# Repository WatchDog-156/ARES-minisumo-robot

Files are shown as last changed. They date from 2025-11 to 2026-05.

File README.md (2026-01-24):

# ARES – Autonomiczny Robot Elektroniczny Sumo

Projekt autonomicznego robota minisumo, budowanego w ramach zajęć z przedmiotu Sterowniki Robotów. Robot przeznaczony jest do rywalizacji na arenie zgodnej z regulaminem Robotic Arena.

---

## Spis treści
- [Opis projektu](#opis-projektu)
- [Architektura systemu](#architektura-systemu)
- [Konfiguracja mikrokontrolera](#konfiguracja-mikrokontrolera)
- [Urządzenia zewnętrzne](#urządzenia-zewnętrzne)
- [Projekt elektroniki](#projekt-elektroniki)
- [Konstrukcja mechaniczna](#konstrukcja-mechaniczna)
- [Oprogramowanie](#oprogramowanie)

---

## Opis projektu

Głównym celem projektu jest zbudowanie w pełni autonomicznego robota mobilnego klasy **MiniSumo**, którego podstawowym zadaniem jest wykrycie przeciwnika na arenie, szybkie dotarcie do niego i wypchnięcie poza białą linię ograniczającą ring. Robot jednocześnie musi samodzielnie unikać wyjechania poza obszar walki.

Robot wykorzystuje system czujników:
- **Czujniki białej linii** – do detekcji krawędzi areny
- **Czujniki odległości IR (ToF)** – do lokalizacji przeciwnika
- **System ASS (Anti-Sumo System)** – serwomechanizmy z białymi ekranami, wprowadzające przeciwnika w błąd

---

## Architektura systemu

System składa się z trzech głównych warstw:

1. **Warstwa sprzętowa** – mikrokontroler, czujniki, silniki, sterowniki, zasilanie
2. **Warstwa sterowania** – oprogramowanie na Raspberry Pi Pico
3. **Warstwa komunikacji** – USART (Bluetooth) do debugowania i monitorowania

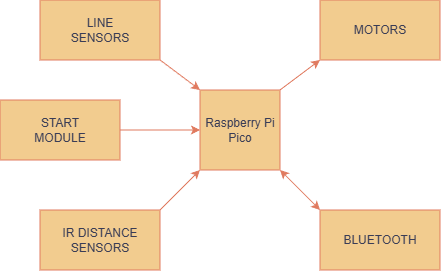
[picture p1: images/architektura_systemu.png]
Architektura systemu


---

## Konfiguracja mikrokontrolera

W projekcie wykorzystano **Raspberry Pi Pico 2 WH** z układem RP2350 (ARM Cortex M33), który oferuje:
- Dwa rdzenie obliczeniowe
- Wbudowany moduł WiFi/Bluetooth (CYW43439)
- Wystarczającą liczbę pinów GPIO
- Niskie zużycie energii

### Konfiguracja pinówdotarcie

| Pin | Tryb pracy | Funkcja |
|-----|---|---|
| 1 | USART0 TX | Wysyłanie danych Bluetooth |
| 2 | USART0 RX | Odbieranie danych Bluetooth |
| 10  | GPIO_Output | Silnik lewy – kierunek "do przodu" |
| 11  | GPIO_Output | Silnik lewy – kierunek "do tyłu" |
| 12  | PWM | Silnik lewy – sygnał PWM |
| 14  | PWM | Silnik prawy – sygnał PWM |
| 15  | GPIO_Output | Silnik prawy – kierunek "do tyłu" |
| 16  | GPIO_Output | Silnik prawy – kierunek "do przodu" |
| 19  | GPIO_Input | Start walki (przycisk/modul startowy) |
| 20  | GPIO_Input | Kill (koniec walki) |
| 21  | GPIO_Output | XSHUT 1 – włącznik czujnika odległości 1 |
| 22  | GPIO_Output | XSHUT 2 – włącznik czujnika odległości 2 |
| 24  | GPIO_Output | XSHUT 3 – włącznik czujnika odległości 3 |
| 25  | GPIO_Output | XSHUT 4 – włącznik czujnika odległości 4 |
| 26  | I2C0 SDA | Dane z czujników odległości IR |
| 27  | I2C0 SCL | Zegar czujników odległości IR |
| 31  | ADC_IN | Prawy czujnik linii (analogowy) |
| 32  | ADC_IN | Lewy czujnik linii (analogowy) |

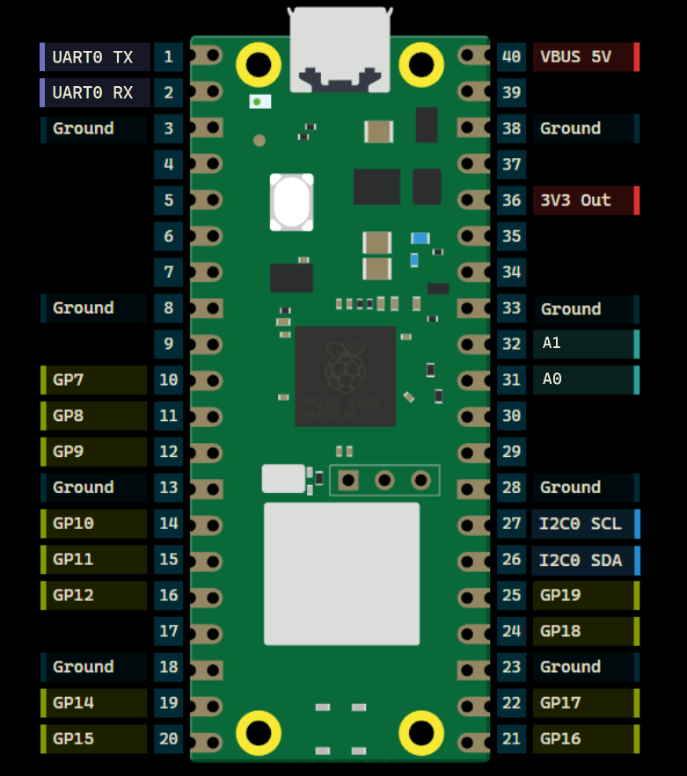
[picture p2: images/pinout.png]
Raspberry Pi Pico 2 WH pinout


### Konfiguracja peryferiów

#### USART (Bluetooth)
- Baud Rate: 115200
- Word Length: 8 bitów
- Parity: Brak
- Stop Bits: 1

#### I2C (czujniki VL53L0X)
- Tryb: Standard Mode
- Częstotliwość: 100 kHz
- Adresowanie: 7-bitowe

#### ADC (czujniki linii)
- Rozdzielczość: 12 bitów
- Tryb: Single Conversion
- Częstotliwość próbkowania: 96 cykli

---

## Urządzenia zewnętrzne

### 3.1 Czujniki białej linii – KTIRO711S
- **Zasilanie:** 5V
- **Wyjście:** analogowe
- **Rodzaj:** odbiciowy fototranzystorowy
- **Rozdzielczość:** 1 mm
- **Zastosowanie:** detekcja białej linii areny

### 3.2 Czujniki odległości IR – VL53L0X
- **Zasilanie:** 3.3 – 5V
- **Zakres pomiarowy:** 2 – 200 cm
- **Częstotliwość odczytu:** do 50 Hz
- **Interfejs:** I2C
- **Kąt widzenia:** 25° stożkowy
- **Ilość:** 4 szt. (2 przednie, 2 skośne)

### 3.3 Sterownik silników – TB6612FNG
- **Napięcie silników:** do 15V
- **Napięcie logiczne:** 2.7 – 5.5V
- **Prąd ciągły:** 1.2A na kanał
- **Prąd szczytowy:** 3.2A
- **Tryby:** CW, CCW, hamulec, stop

### 3.4 Silniki DC – N20-BT37 210:1 140RPM
- **Napięcie:** 3 – 9V
- **Przekładnia:** 210:1
- **Prędkość:** 140 RPM
- **Moment obrotowy:** 3.6 kg·cm

### 3.5 Serwomechanizmy – MG90S Mikro (ASS)
- **Napięcie:** 4.8V
- **Kąt obrotu:** 180°
- **Moment:** 2 kg·cm
- **Zastosowanie:** system wprowadzania w błąd przeciwnika

### 3.6 Moduł startowy MiniSumo
- **Funkcja:** detekcja startu walki
- **Zapobiega falstartom**
- **Wymagany na zawodach**

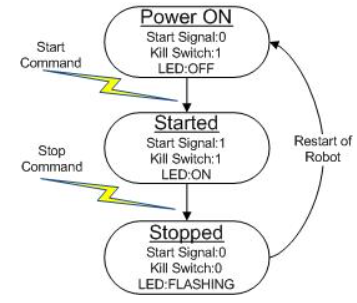
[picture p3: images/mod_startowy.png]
Moduł startowy


---

## Projekt elektroniki

Zaprojektowano dedykowaną płytkę PCB w formie shielda dla Raspberry Pi Pico, która integruje wszystkie komponenty:

### Główne cechy projektu:
- Zasilanie z baterii LiPo 7.4V
- Stabilizator napięcia 5V dla logiki i czujników
- Filtracja napięć i zabezpieczenia przeciwprzepięciowe
- Wyprowadzenia dla wszystkich czujników i silników
- Łatwy montaż na robocie

### Schematy i projekty:

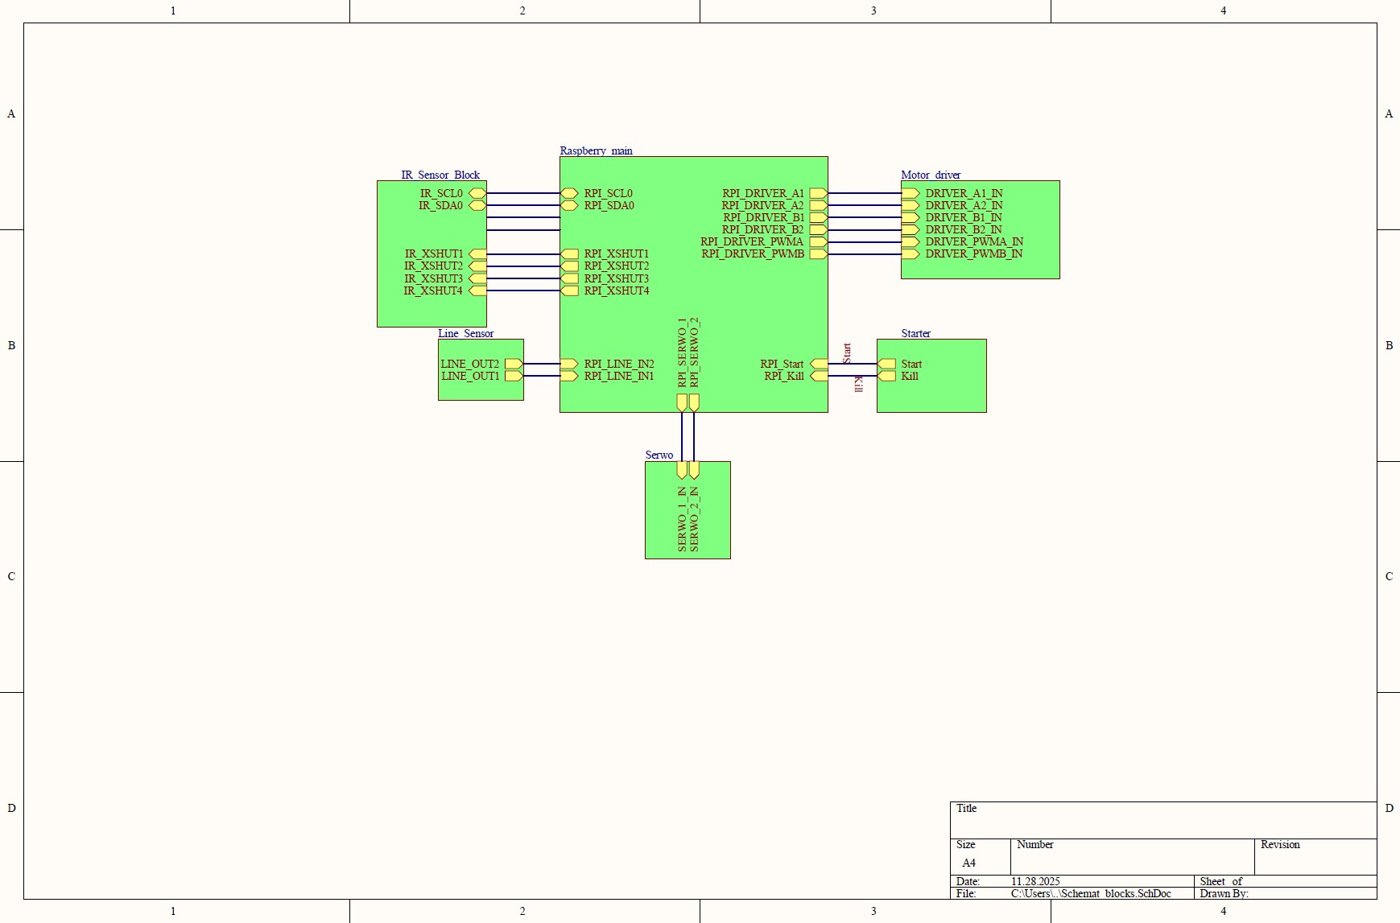
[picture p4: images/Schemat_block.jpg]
Schemat blokowy PCB


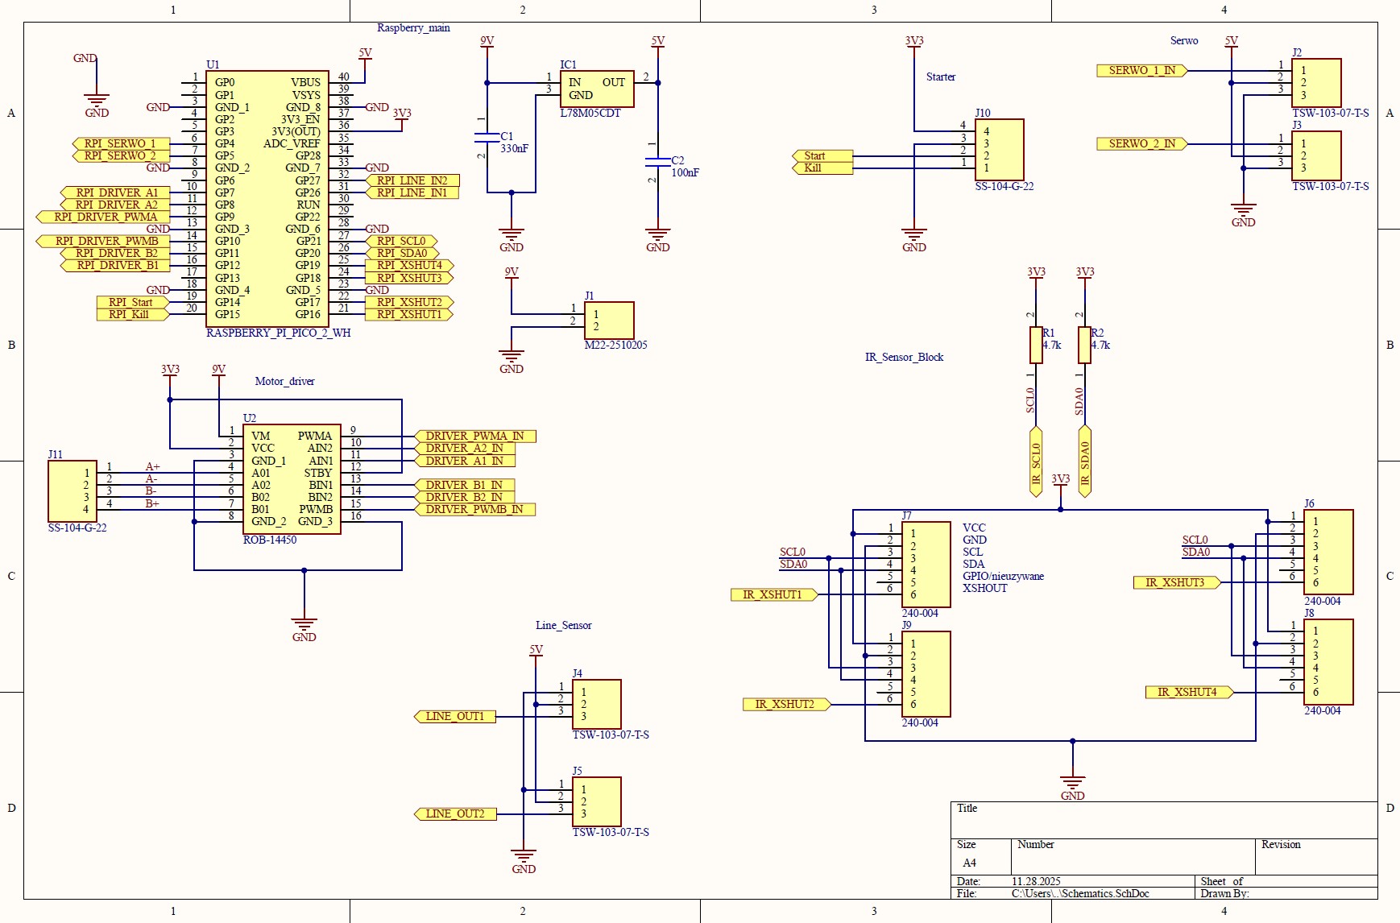
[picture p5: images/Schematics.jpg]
Schemat elektroniczny


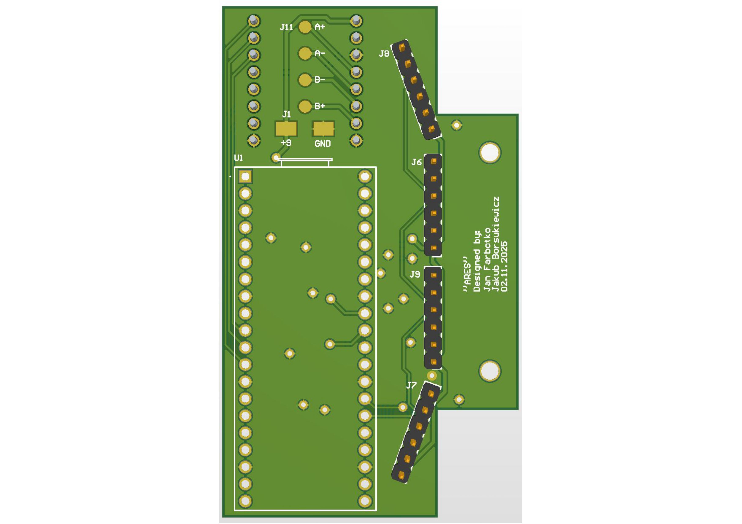
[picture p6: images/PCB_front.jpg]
Projekt PCB – warstwa górna


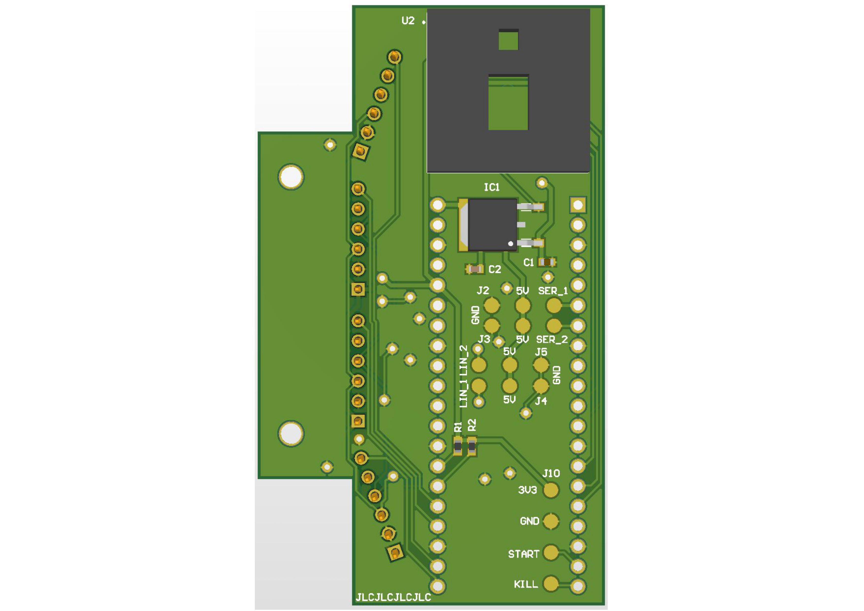
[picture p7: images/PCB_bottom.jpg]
Projekt PCB – warstwa dolna


### Montaż i lutowanie:

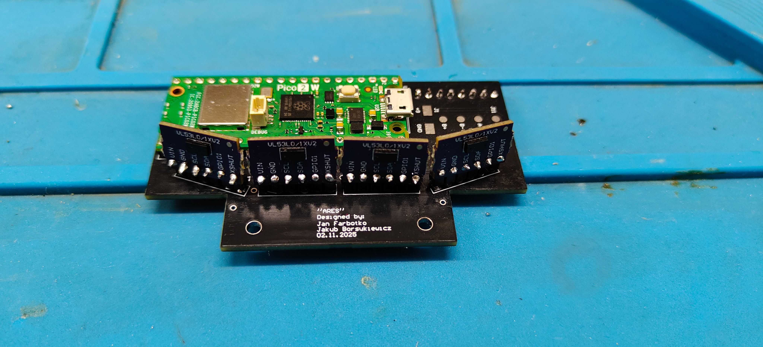
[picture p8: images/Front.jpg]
PCB po lutowaniu – przód


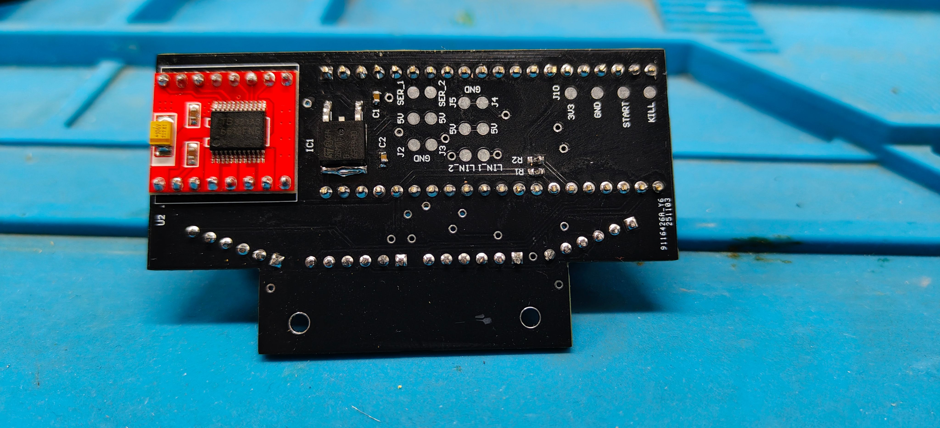
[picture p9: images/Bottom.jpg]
PCB po lutowaniu – tył


---

## Konstrukcja mechaniczna

### Projekt CAD
Konstrukcja zaprojektowana w **Autodesk Inventor**, składa się z:
- Głównej obudowy (korpus)
- Pokrywy górnej
- Dwóch części plugów
- Kół z felgami 3D i oponami silikonowymi

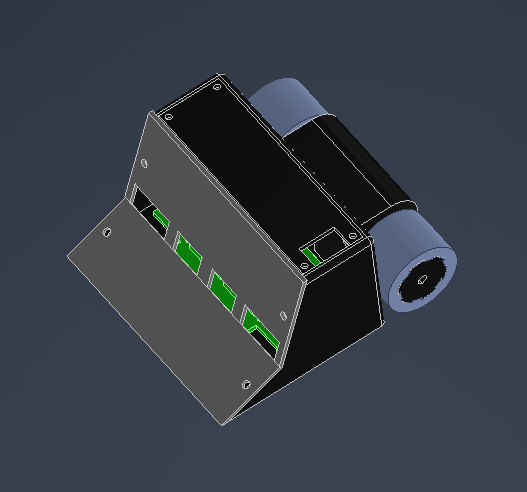
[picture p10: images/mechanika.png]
Model 3D robota


### Produkcja
- Wydruk 3D z filamentu PET-G
- Wstawki mosiężne do mocowania
- Śruby metalowe M3 oraz M2.5
- Opony z silikonu formierskiego

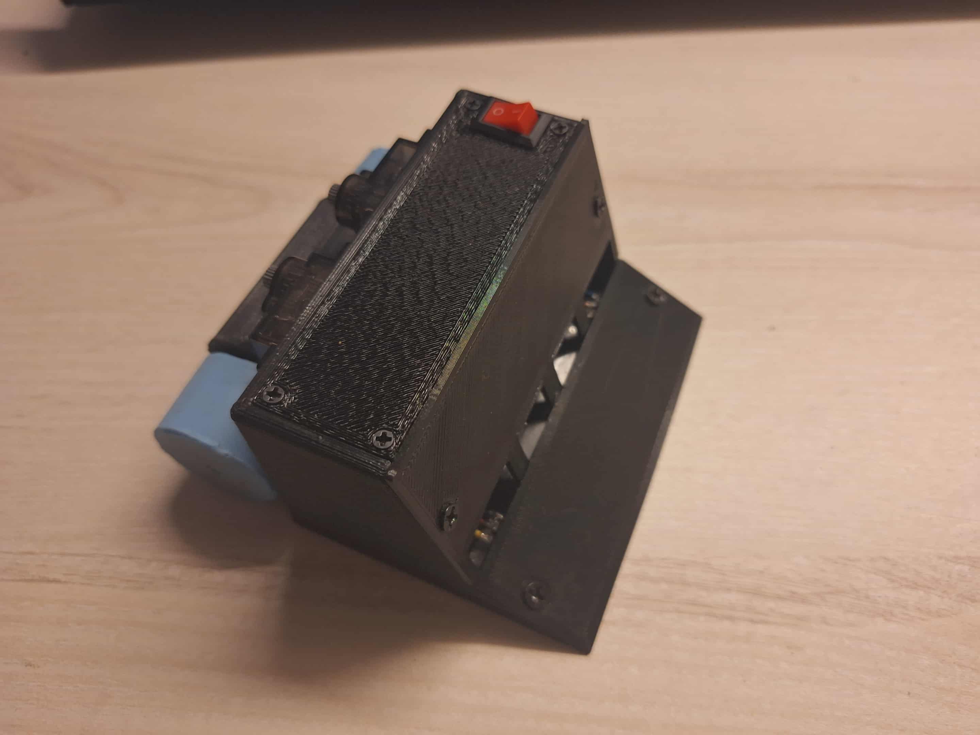
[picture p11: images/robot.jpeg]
Gotowy robot


---

## Oprogramowanie

Głównym zadaniem działania programu dla robota minisumo jest realizacja autonomicznego cyklu walki. Robot ma za zadanie odpowiednio przetwarzać otrzymywane dane z czujników odległości i linii, na które odpowiednio reaguje poprzez jazdę w zadanym kierunku. 

### Logika programu
Logika programu została podzielona na odpowiednie stany:
- Start - po uruchomieniu robota, następuje inicjalizacja wszystkich czujników i urządzeń; czujniki zbierające dane zaczynają swoją pracę.
- Walka - następuje po odpowiednim zadaniu sygnału przez moduł startowy; robot przetwarza otrzymane dane z czujników i zadaje odpowiednie sterowanie do silników w zależności od podjętej strategii.
- Koniec - po zadaniu odpowiedniego sygnału przez moduł startowy praca robota jest zatrzymywana.

Diagram blokowy na rysunku:
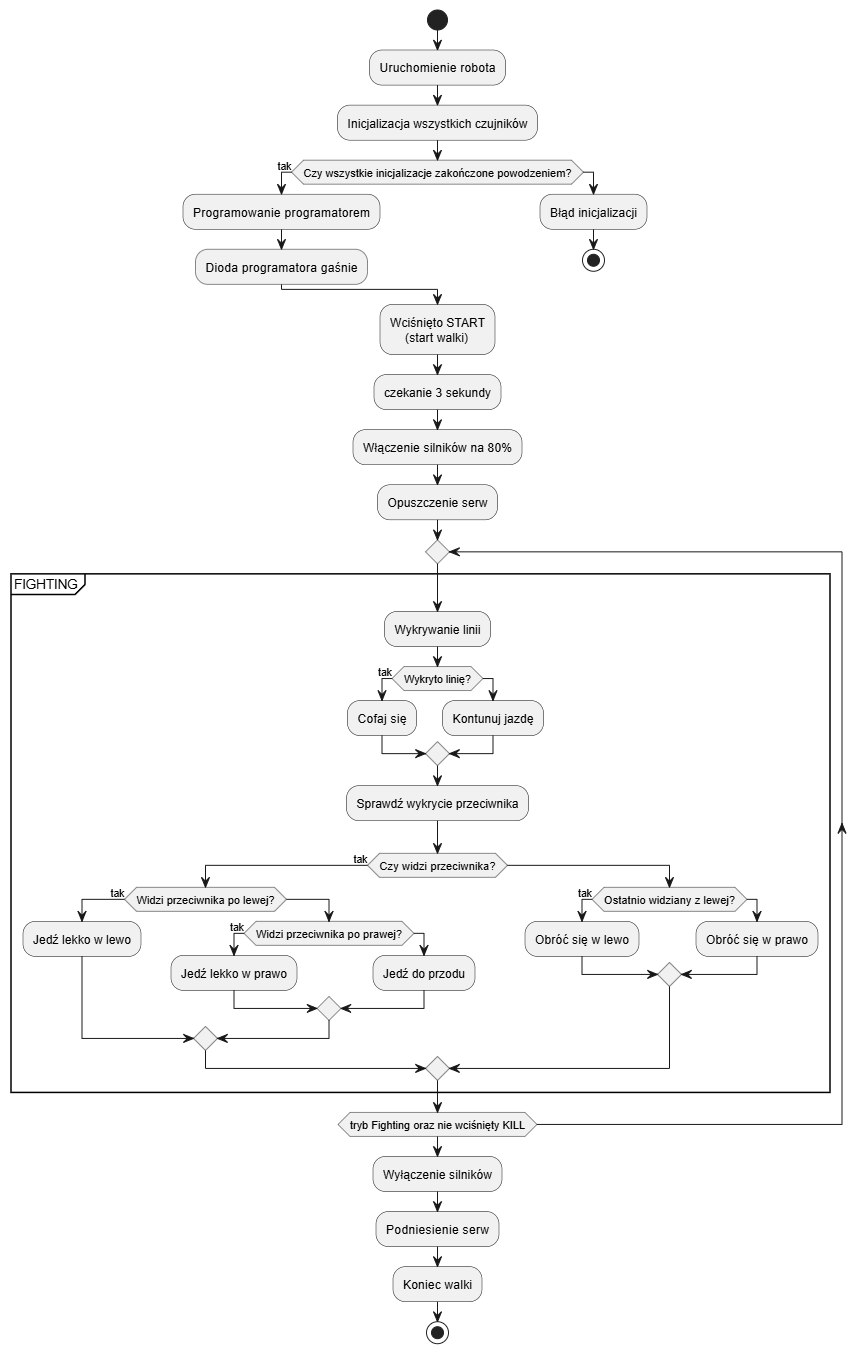
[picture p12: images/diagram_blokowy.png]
Diagram blokowy algorytmu robota


### Bluetooth
Funkcja Bluetooth nie jest elementem wymaganym, aby program robota minisumo działał. Mimo to jest to aspekt, który ułatwia pracę. Bluetooth działa w dwie strony. Z jednej pozwala na łatwy odczyt danych z czujników, co eliminuje potrzebę podłączenia robota do urządzenia z terminalem np.komputera. Z drugiej strony dzięki urządzeniu posiadającemu zwykłą aplikacje do obsługi terminala z bluetooth np.telefon jesteśmy również w stanie zadać robotowi odpowiednie komunikaty, które on obsługuje np. jazda do przodu z określoną prędkością. 

### Czujniki odległości
Czujników odległości to jedne z najważniejszych aspektów pracy całego oprogramowania robota minisumo. To właśnie te czujniki decydują, w którą stronę powinien poruszyć się robot w danym czasie. W implementacji użyto 4 czujników, które działają na jednej magistrali I2C. Aby można było odczytywać informacje z każdego z nich osobno należy odpowiednio nadać adresy dla każdego z czujników. Wszystkie czujniki są wyłączane poprzez ich piny XSHUT, następnie każdy z nich jest pojedynczo włączany i zostaje mu zmieniony adres. Każdy z nich jest ustawiany, aby działać odpowiednio jak założył producent (w tym celu posłużono się gotowymi funkcjami kalibrującymi czujniki). 

### Czujniki linii
Czujniki linii to ważny element oprogramowania robota minisumo. To one odpowiadają za to, że robot samoistnie nie wyjedzie za obszar ringu. Ich implementacja nie należy do najtrudniejszej - czujniki wykrywają czy odczytana wartość z przetwornika ADC zmieniła się po najechaniu robota na obszar białej linii i nie wyniosła wartości poniżej zadanej. W przypadku wykrycia zostaje wykonana odpowiednia akcja.

### Silniki
Program silników odpowiada za aspekt poruszania się robota w założonym kierunku z odpowiednią prędkością. Jest to element, który wykonuje polecenia zadane przez logikę i przyjętą strategię po przetworzeniu danych z czujników. Prędkość obrotu silników jest sterowana za pomocą PWM. Dzięki odpowiednim funkcją można odpowiednio przeskalować wartości tak, aby zadawać wypełnienie liczbami z przedziału [0-100\%]. 

W robocie znajdują się dwa silniki, gdzie każdy jest sterowany osobnym sygnałem PWM oraz każdy z nich ma również po dwa wejścia logiczne (dir1 i dir2). To właśnie od tych pinów zależy w którą stronę będzię obracać się silniki. Zadanie na jeden z nich stanu wysokiego a na drugi niskiego spowoduje obracanie się silnika w odpowiednią stronę. Gdy oba piny otrzymają stan niski, to silniki się zatrzymają - stop (Luz). W przypadku gdy oba stany będą wysokie - hamulec. 

### Serwa
Ten aspekt został opracowany dodatkowo, ale jest jednym z założeń strategicznych robota minisumo. Na robocie zamontowano dwa serwa, a na ich końcach cienkie "skrzydła". Po wystartowaniu walki serwa są opuszczane co powoduje, że robotowi przybywa na wielkości - przeciwnik wykrywa przeszkodę, która nie jest sam robot co może dać przewagę. Serwa tak jak silniki są sterowane przez PWM. Jednak różnica jest taka, tutaj zadajemy pozycję (kąt) w jakim ma ustawić się sprzęt. Zależy to oczywiście od wypełnienia - proporcji czasu trwania impulsu wysokiego do całego czasu okresu trwania sygnału. Aby uprościć to odpowiednio przeliczono te wartości na stopnie. Z dokumentacji wyczytano, że częstotliwość pracy serwa wynosi 50Hz, a to pozwoliło określić jaki czas trwania okresu to jaki kąt pozycji serwa. 

### Starter
Starter to zwykła maszyna stanów. Jest to odbiornik do programatora, który pozwala na sprawiedliwe jednoczesne wystartowanie obu robotów podczas zawodów. Piny logiczne startera po zaprogramowaniu go przyjmują odpowiednio stany: Start - 0, Kill - 1. Następnie gdy programator wystartuje walkę stany zmieniają się odpowiednio na (1,1) - następuje walka. Gdy programator wywoła sygnał stopu - oba stany pinów przyjmą odpowiednio (0,0) - co powoduje zatrzymanie robotów. 

---

**Autorzy:** Jakub BORSUKIEWICZ, Jan FARBOTKO

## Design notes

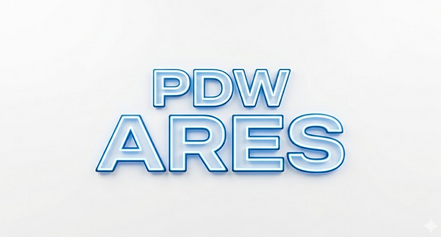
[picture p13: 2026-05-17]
data_visualization_app/img/ikonka.png

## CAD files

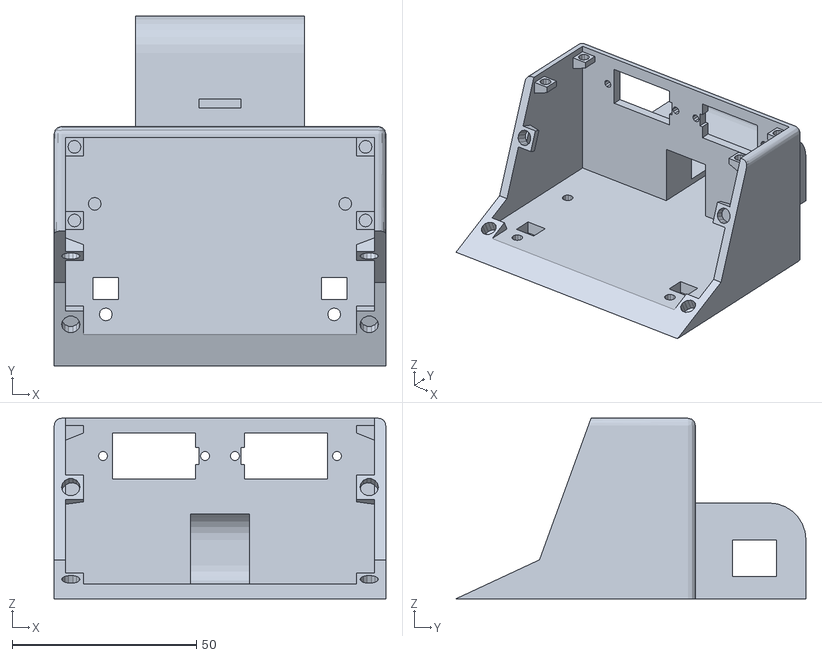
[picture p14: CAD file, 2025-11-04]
mechanics/stl_files/obudowa_robota.stl
90.0 x 95.0 x 49.0

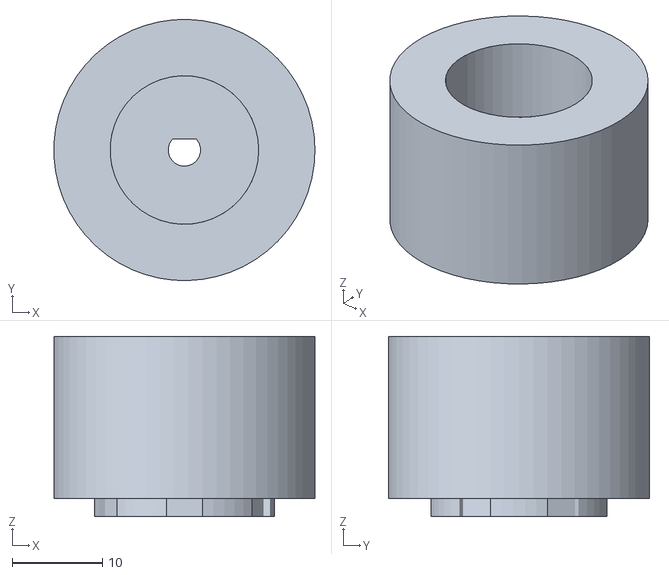
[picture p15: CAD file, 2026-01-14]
ros2/src/ARES_robot_model/meshes/wheel.STL
29.0 x 29.0 x 20.0

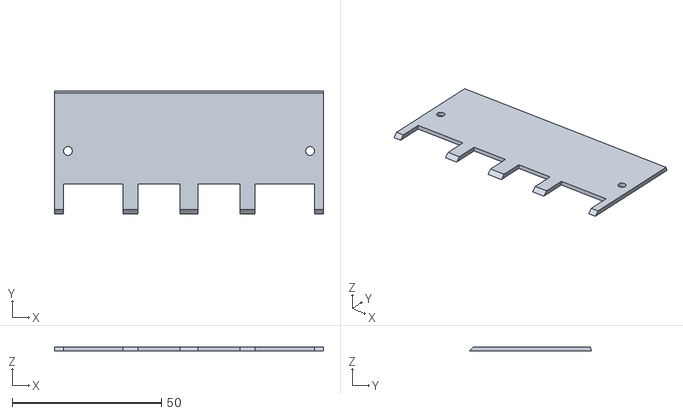
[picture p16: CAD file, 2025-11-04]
mechanics/stl_files/pług_część2.stl
90.0 x 41.0 x 1.50

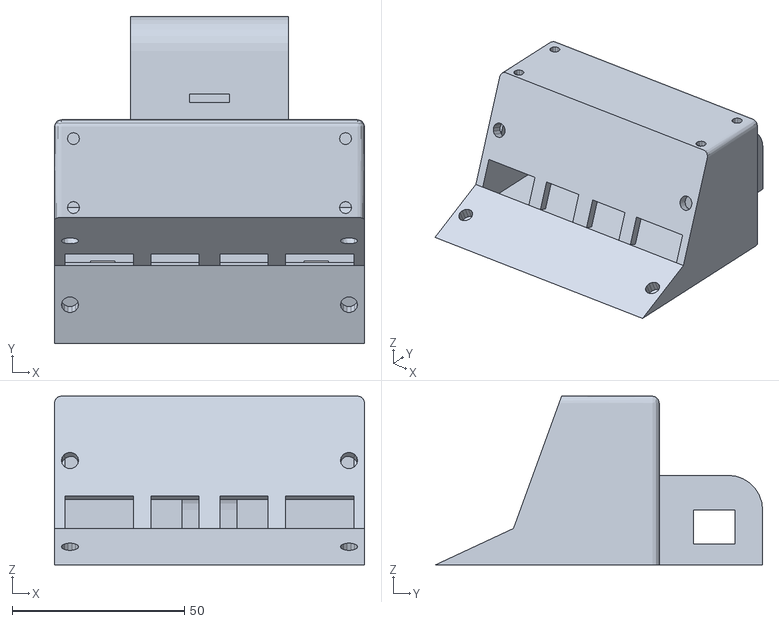
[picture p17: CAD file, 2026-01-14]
ros2/src/ARES_robot_model/meshes/body.STL
90.0 x 95.0 x 49.0

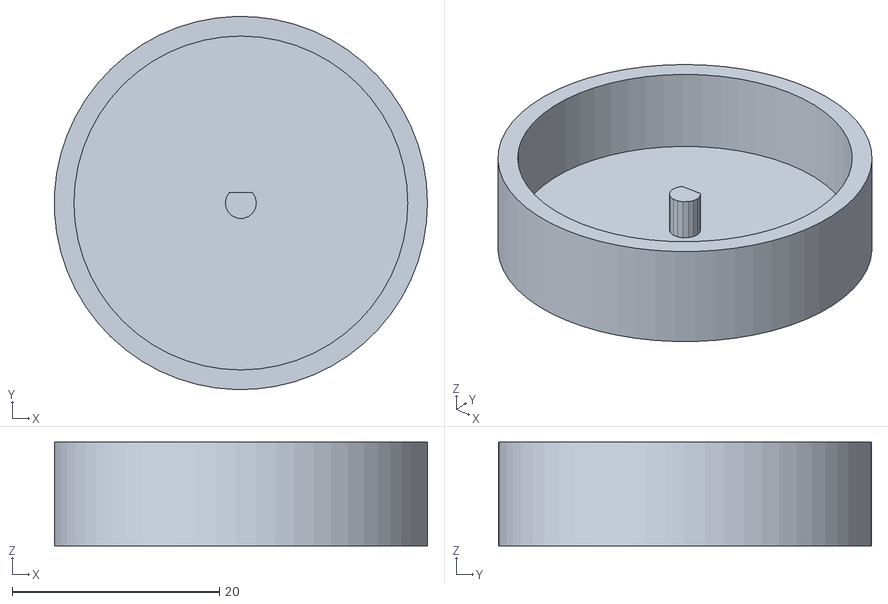
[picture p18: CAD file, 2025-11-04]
mechanics/stl_files/forma_do_kół.stl
36.0 x 36.0 x 10.0

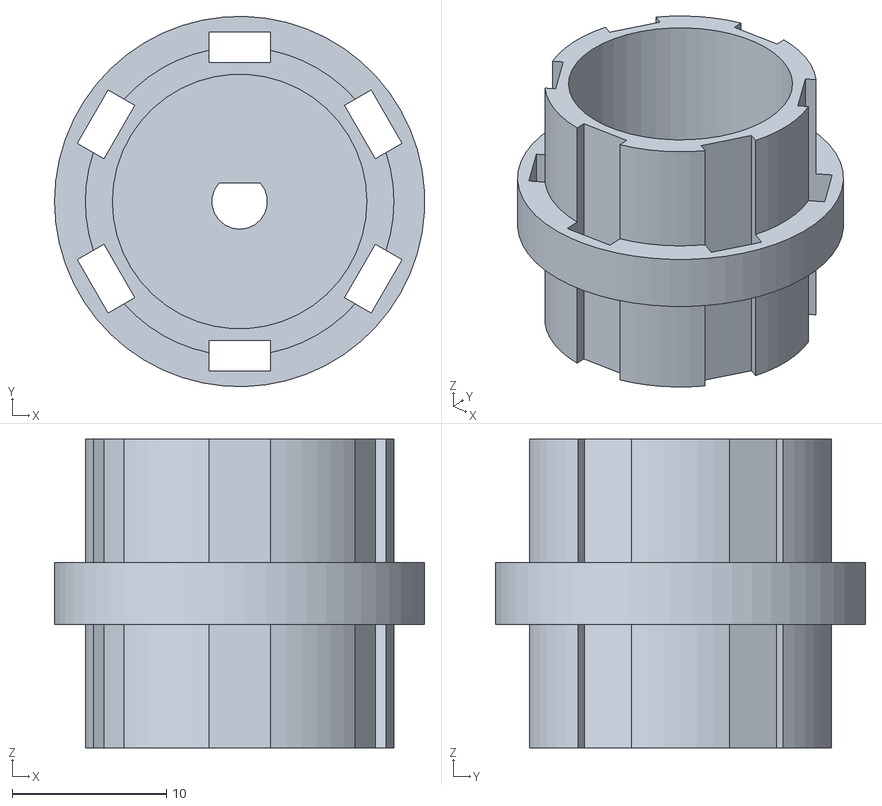
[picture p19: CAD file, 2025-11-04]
mechanics/stl_files/koło.stl
24.0 x 24.0 x 20.0

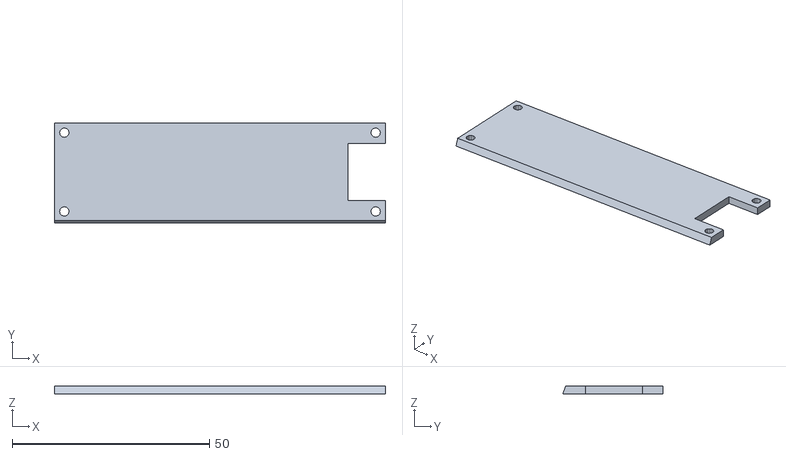
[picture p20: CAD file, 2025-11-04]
mechanics/stl_files/góra_robota.stl
84.0 x 25.5 x 2.00

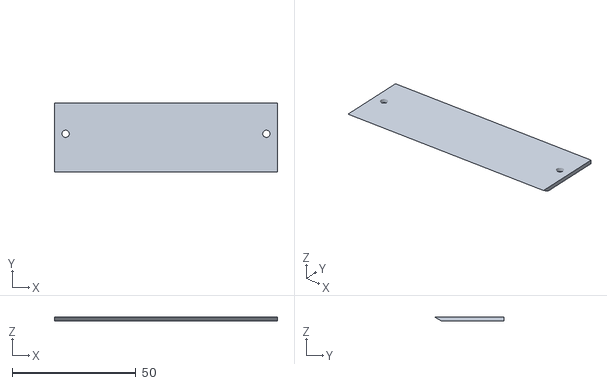
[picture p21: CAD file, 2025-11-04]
mechanics/stl_files/pług_część1.stl
90.0 x 28.0 x 1.50

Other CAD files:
mechanics/forma_do_kół.ipt
mechanics/góra_robota.ipt
mechanics/koło.ipt
mechanics/minisumo_złożenie.iam
mechanics/obudowa_robota.ipt
mechanics/opona.ipt
mechanics/pług_część1.ipt
mechanics/pług_część2.ipt
mechanics/płytka_pcb.ipt

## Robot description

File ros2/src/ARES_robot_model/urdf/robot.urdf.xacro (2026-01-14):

<?xml version="1.0"?>
<robot name="ARES_robot_model" xmlns:xacro="http://www.ros.org/wiki/xacro">
    
    <!--Wymiary robota-->
    <xacro:property name="bodyWidth" value="0.09"/>
    <xacro:property name="bodyLength" value="0.1"/>
    <xacro:property name="bodyHeight" value="0.05"/>
    <xacro:property name="wheelRadius" value="0.0145"/>

    <!--Kolory-->
    <material name="red">
        <color rgba="0.8 0.0 0.0 1.0"/>
    </material>
    <material name="blue">
        <color rgba="0.0 0.0 0.8 0.75"/>
    </material>
    <material name="green">
        <color rgba="0.0 0.8 0.0 1.0"/>
    </material>

    <!--Makro do inercji-->
    <xacro:macro name="default_inertial" params="mass">
        <inertial>
            <mass value="${mass}" />
            <inertia ixx="1e-3" ixy="0.0" ixz="0.0" iyy="1e-3" iyz="0.0" izz="1e-3" />
        </inertial>
    </xacro:macro>

    <!--Bryła robota-->
    <link name="body">
        <visual>
            <origin xyz="0.0 0.0 0.0" rpy="0.0 0.0 ${pi/2}"/>
            <geometry>
                <mesh filename="file://$(find ARES_robot_model)/meshes/body.STL" scale="0.001 0.001 0.001"/>
            </geometry>
            <material name="blue"/>
        </visual>
        <collision>
            <origin xyz="${-bodyLength/2} 0.0 ${bodyHeight/2}" rpy="0.0 0.0 ${pi/2}"/>
            <geometry>
                <box size="${bodyLength} ${bodyWidth} ${bodyHeight}"/>
            </geometry>
        </collision>
        <xacro:default_inertial mass="0.3"/>
    </link>

    <!--Lewe koło-->
    <link name="left_wheel">
        <visual>
            <origin xyz="0.0 0.01 0.0" rpy="${pi/2} 0.0 0.0"/>
            <geometry>
                <mesh filename="file://$(find ARES_robot_model)/meshes/wheel.STL" scale="0.001 0.001 0.001"/>
            </geometry>
            <material name="red"/>
        </visual>
        <collision>
            <origin xyz="0.0 0.01 0.0" rpy="${pi/2} 0.0 0.0"/>
            <geometry>
                <cylinder radius="${wheelRadius}" length="0.02"/>
            </geometry>
        </collision>
        <xacro:default_inertial mass="0.1"/>
    </link>
    <joint name="left_wheel_joint" type="continuous">
        <parent link="body"/>
        <child link="left_wheel"/>
        <origin xyz="${0.015-bodyLength} 0.035 0.01" rpy="0.0 0.0 0.0"/>
        <axis xyz="0.0 1.0 0.0"/>
        <limit effort="100" velocity="10.0"/>
        <dynamics damping="0.1" friction="0.1"/>
    </joint>

    <!--Prawe koło-->
    <link name="right_wheel">
        <visual>
            <origin xyz="0.0 -0.01 0.0" rpy="${-pi/2} 0.0 0.0"/>
            <geometry>
                <mesh filename="file://$(find ARES_robot_model)/meshes/wheel.STL" scale="0.001 0.001 0.001"/>
            </geometry>
            <material name="red"/>
        </visual>
        <collision>
            <origin xyz="0.0 -0.01 0.0" rpy="${-pi/2} 0.0 0.0"/>
            <geometry>
                <cylinder radius="${wheelRadius}" length="0.02"/>
            </geometry>
        </collision>
        <xacro:default_inertial mass="0.1"/>
    </link>
    <joint name="right_wheel_joint" type="continuous">
        <parent link="body"/>
        <child link="right_wheel"/>
        <origin xyz="${0.015-bodyLength} -0.035 0.01" rpy="0.0 0.0 0.0"/>
        <axis xyz="0.0 1.0 0.0"/>
        <limit effort="100" velocity="10.0"/>
        <dynamics damping="0.1" friction="0.1"/>
    </joint>

    <!--LIDAR-->
    <link name="lidar">
        <visual>
            <origin xyz="0.0 0.0 0.0" rpy="0.0 ${-pi/16} 0.0"/>
            <geometry>
                <box size="0.005 0.08 0.02"/>
            </geometry>
            <material name="green"/>
        </visual>
        <collision>
            <origin xyz="0.0 0.0 0.0" rpy="0.0 ${-pi/16} 0.0"/>
            <geometry>
                <box size="0.005 0.08 0.02"/>
            </geometry>
        </collision>
        <xacro:default_inertial mass="0.03"/>
    </link>
    <joint name="lidar_joint" type="fixed">
        <parent link="body"/>
        <child link="lidar"/>
        <origin xyz="-0.033 0.0 0.014" rpy="0.0 ${-pi/32} 0.0"/>
    </joint>

    <!--Skrzydlo lewe-->
    <link name="left_wing">
        <visual>
            <origin xyz="-0.0025 0.095 0.0" rpy="0.0 0.0 0.0"/>
            <geometry>
                <box size="0.005 0.2 0.015"/>
            </geometry>
            <material name="green"/>
        </visual>
        <visual>
            <origin xyz="-0.0025 0.115 -0.02" rpy="0.0 0.0 0.0"/>
            <geometry>
                <box size="0.005 0.16 0.025"/>
            </geometry>
            <material name="green"/>
        </visual>
        <collision>
            <origin xyz="-0.0025 0.095 0.0" rpy="0.0 0.0 0.0"/>
            <geometry>
                <box size="0.005 0.2 0.015"/>
            </geometry>
        </collision>
        <collision>
            <origin xyz="-0.0025 0.115 -0.02" rpy="0.0 0.0 0.0"/>
            <geometry>
                <box size="0.005 0.16 0.025"/>
            </geometry>
        </collision>
        <xacro:default_inertial mass="0.01"/>
    </link>
    <joint name="left_wing_joint" type="fixed">
        <parent link="body"/>
        <child link="left_wing"/>
        <origin xyz="-0.068 0.014 0.04" rpy="0.0 0.0 0.0"/>
    </joint>

    <!--Skrzydlo prawo-->
    <link name="right_wing">
        <visual>
            <origin xyz="-0.0025 -0.095 0.0" rpy="0.0 0.0 0.0"/>
            <geometry>
                <box size="0.005 0.2 0.015"/>
            </geometry>
            <material name="green"/>
        </visual>
        <visual>
            <origin xyz="-0.0025 -0.115 -0.02" rpy="0.0 0.0 0.0"/>
            <geometry>
                <box size="0.005 0.16 0.025"/>
            </geometry>
            <material name="green"/>
        </visual>
        <collision>
            <origin xyz="-0.0025 -0.095 0.0" rpy="0.0 0.0 0.0"/>
            <geometry>
                <box size="0.005 0.2 0.015"/>
            </geometry>
        </collision>
        <collision>
            <origin xyz="-0.0025 -0.115 -0.02" rpy="0.0 0.0 0.0"/>
            <geometry>
                <box size="0.005 0.16 0.025"/>
            </geometry>
        </collision>
        <xacro:default_inertial mass="0.01"/>
    </link>
    <joint name="right_wing_joint" type="fixed">
        <parent link="body"/>
        <child link="right_wing"/>
        <origin xyz="-0.068 -0.014 0.04" rpy="0.0 0.0 0.0"/>
    </joint>

    <!-- Include pliku Gazebo lidar oraz differential drive controller-->
    <xacro:include filename="$(find ARES_robot_model)/urdf/configurations.gazebo.xml"/>
    <xacro:include filename="$(find ARES_robot_model)/urdf/lidar.gazebo.xml"/>
    <xacro:include filename="$(find ARES_robot_model)/urdf/differential_drive.gazebo.xml"/>

</robot>

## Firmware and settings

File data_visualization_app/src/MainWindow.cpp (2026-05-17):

/**
 * @file MainWindow.cpp
 * @author Jakub Borsukiewicz & Jan Farbotko
 * @brief Tworzy główne okno aplikacji oraz zarządza działaniem przycisków
 * @version 1.0
 * @date 2026-05-05
 * 
 * @copyright Copyright (c) 2026
 * 
 */
#include "MainWindow.hpp"
#include "./ui_MainWindow.h"
#include <QDebug>
#include <QApplication>

/**
 * @brief Inicjalizuje główne okno aplikacji, komponenty UI oraz menedżery komunikacji
 * 
 * Tworzy instancję interfejsu użytkownika, konfiguruje wykresy ToF i linii, 
 * inicjalizuje menedżera Bluetooth oraz ustawia domyślny widok aplikacji
 * @param[in] parent - wskaźnik na obiekt rodzica
 */
MainWindow::MainWindow(QWidget *parent)
    : QMainWindow(parent)
    , ui(new Ui::MainWindow)
{
    ui->setupUi(this);

    ui->EnterText->clear();
    ui->EnterText->setPlaceholderText(tr("enter text..."));
      
    bluetoothManager = new BluetoothManager(this);
    bluetoothLogger = nullptr;
    bluetoothScanner = new BluetoothScanner(this);

    ui->RobotDiagram->setCheckable(true);
    ui->TofDiagram->setCheckable(true);
    ui->LineDiagram->setCheckable(true);
    ui->RoadDiagram->setCheckable(true);
    

    robot = new RobotDiagram(this);
    ui->stackedWidget->insertWidget(0, robot);
    tof = new ToFChart(this);
    ui->stackedWidget->insertWidget(1, tof);
    line = new LineChart(this);
    ui->stackedWidget->insertWidget(2, line);
    road = new TrajectoryWidget(this);
    ui->stackedWidget->insertWidget(3, road);
    robotPicture = new RobotPicture(this);
    ui->stackedWidget->insertWidget(4, robotPicture);
    ui->stackedWidget->addWidget(robotPicture);
    ui->stackedWidget->setCurrentWidget(robotPicture);

    setupConnections();
    this->setWindowTitle(tr("ARES Visual Data Panel"));
}

/**
 * @brief Destruktor klasy MainWindow
 * 
 * Zwalnia zasoby zajmowane przez interfejs użytkownika oraz powiązane obiekty
 */
MainWindow::~MainWindow()
{
    delete ui;
}

/**
 * @brief Funckja konfigurująca połączenia sygnałów i slotów
 * 
 * Funkcja odpowiada za połaczenia interfejsu (kliknięcie przycisku, zatwierdzenie tekstu) 
 * z odpowiednimi metodami obsługi zdarzeń
 */
void MainWindow::setupConnections(){
    connect(ui->ButtonStart, &QPushButton::clicked, this, &MainWindow::handleCommandButtons);
    connect(ui->ButtonStop, &QPushButton::clicked, this, &MainWindow::handleCommandButtons);
    connect(ui->ButtonForward, &QPushButton::clicked, this, &MainWindow::handleCommandButtons);
    connect(ui->ButtonBackward, &QPushButton::clicked, this, &MainWindow::handleCommandButtons);
    connect(ui->ButtonServoUp, &QPushButton::clicked, this, &MainWindow::handleCommandButtons);
    connect(ui->ButtonServoDown, &QPushButton::clicked, this, &MainWindow::handleCommandButtons);
    connect(ui->ButtonEND, &QPushButton::clicked, this, &MainWindow::handleCommandButtons);
    connect(ui->EnterText, &QLineEdit::returnPressed, this, &MainWindow::handleManualCommands);
    connect(ui->Language, &QComboBox::currentIndexChanged, this, &MainWindow::handleLanguage);
    connect(ui->RoadDiagram, &QPushButton::clicked, this, &MainWindow::handleFunctionButtons);
    connect(ui->Log, &QPushButton::clicked, this, &MainWindow::handleFunctionButtons);
    connect(ui->Connection, &QPushButton::clicked, this, &MainWindow::handleFunctionButtons);
    connect(ui->RobotDiagram, &QPushButton::clicked, this, &MainWindow::handleFunctionButtons);
    connect(ui->TofDiagram, &QPushButton::clicked, this, &MainWindow::handleFunctionButtons);
    connect(ui->LineDiagram, &QPushButton::clicked, this, &MainWindow::handleFunctionButtons);
    connect(bluetoothManager, &BluetoothManager::dataReceived, this, &MainWindow::onDataReceived);
    connect(bluetoothManager, &BluetoothManager::connectionStatusChanged, this, &MainWindow::onConnectionStatusChanged);
    connect(bluetoothScanner, &BluetoothScanner::deviceSelected, this, &MainWindow::connectToDevice);
    
}

/**
 * @brief Funckja do wysyłania poleceń sterujących do robota przez Bluetooth
 * 
 * Funkcja odpowiada za identyfikajce klikniętego przycisku i wysłanie odpowiadającegomu kodu sterującego
 * za pomoca bluetoothManager
 */
void MainWindow::handleCommandButtons(){
    QPushButton* button = qobject_cast<QPushButton*>(sender());

    if(button == ui->ButtonForward){
        qDebug() << "Forward";
        bluetoothManager->writeData("FWD");
        if(bluetoothLogger)
            bluetoothLogger->addSendedLog("FWD");
    } else if (button == ui->ButtonBackward){
        qDebug() << "Backward";
        bluetoothManager->writeData("BWD");
        if(bluetoothLogger)
            bluetoothLogger->addSendedLog("BWD");
    } else if (button == ui->ButtonStart){
        qDebug() << "Start";
        bluetoothManager->writeData("START");
        if(bluetoothLogger)
            bluetoothLogger->addSendedLog("START");
    } else if (button == ui->ButtonStop){
        qDebug() << "Stop";
        bluetoothManager->writeData("STOP");
        if(bluetoothLogger)
            bluetoothLogger->addSendedLog("STOP");
    } else if (button == ui->ButtonServoUp){
        qDebug() << "ServoUp";
        bluetoothManager->writeData("SER_UP");
        if(bluetoothLogger)
            bluetoothLogger->addSendedLog("SER_UP");
    } else if (button == ui->ButtonServoDown){
        qDebug() << "ServoDown";
        bluetoothManager->writeData("SER_DW");
        if(bluetoothLogger)
            bluetoothLogger->addSendedLog("SER_DW");
    } else if (button == ui->ButtonEND){
        qDebug() << "End";
        bluetoothManager->writeData("END");
        if(bluetoothLogger)
            bluetoothLogger->addSendedLog("END");
    }
}

/**
 * @brief Funckja do wysyłania własnych komend
 * 
 * Funckja odpowiada za wysłanie napisanego ręcznie polecenia przez bluetooth i czyści pole po wysłaniu
 */
void MainWindow::handleManualCommands(){
    QString cmd = ui->EnterText->text();
    if (cmd.isEmpty()) return;
    qDebug() << "Wyslanie komendy: " << cmd;
    bluetoothManager->writeData(cmd);
    if(bluetoothLogger)
        bluetoothLogger->addSendedLog(cmd);
    ui->EnterText->clear();
}

/**
 * @brief Funckja do obsługi przycisków funkcyjnych
 * 
 * Funkcja odpowiada za przyciski funkcjyjne w tym: łaczenie/rozłączanie urządzenie poprzez bluetooth, zmiana okna wyświelającego dane,
 * wyświetlanie logów
 */
void MainWindow::handleFunctionButtons(){
    QPushButton* button = qobject_cast<QPushButton*>(sender());
    if(!button) return;

    if(button == ui->Connection){
        if(isConnected){
            qDebug() << "Disconnecting device";
            bluetoothManager->disconnectDevice();
        }else{
            qDebug() << "Go to Bluetooth Scanner";
            bluetoothScanner->exec();
        }
        return;
    }

    if(button == ui->Log){
        if (!bluetoothLogger) {
            bluetoothLogger = new BluetoothLogger(this);
            bluetoothLogger->setAttribute(Qt::WA_DeleteOnClose);
            connect(bluetoothLogger, &QObject::destroyed, this, [this]() {bluetoothLogger = nullptr;});
        }
        bluetoothLogger->show();
        bluetoothLogger->raise();    
        bluetoothLogger->activateWindow();
    }

    ui->RobotDiagram->setChecked(false);
    ui->TofDiagram->setChecked(false);
    ui->LineDiagram->setChecked(false);
    ui->RoadDiagram->setChecked(false);
    button->setChecked(true);

    if (button == ui->RobotDiagram) ui->stackedWidget->setCurrentIndex(0);
    else if (button == ui->TofDiagram) ui->stackedWidget->setCurrentIndex(1);
    else if (button == ui->LineDiagram) ui->stackedWidget->setCurrentIndex(2);
    else if (button == ui->RoadDiagram) ui->stackedWidget->setCurrentIndex(3); //zmiana na RoadDiagram


    updateButtonStates();
}

/**
 * @brief Funckcja aktualizująca wygląd przycisków wyboru wykresów
 * 
 * Funkcja odpowiada za zmienianie grafiki przycisków (przezroczystości i tła) w zależności od ich stanu 
 */
void MainWindow::updateButtonStates(){
    QList<QPushButton*> buttons = {ui->RobotDiagram, ui->TofDiagram, ui->LineDiagram, ui->RoadDiagram};
    QStringList colors = {"52, 152, 219", "241, 196, 15", "255, 107, 129", "52, 25, 219"};

    for (int i=0; i< buttons.size(); i++){
        double alpha = buttons[i]->isChecked() ? 1.0 : 0.5;
        buttons[i]->setStyleSheet(QString("background-color: rgba(%1, %2); "
                                          "color: black; "
                                          "border: 2px solid black; "
                                          "border-radius: 5px; "
                                          "font-size: 12px; "
                                          "font-weight: bold")
                                .arg(colors[i])
                                .arg(alpha));
    }
}

/**
 * @brief Funkcja do wczytywania wybranego języka aplikacji
 * 
 * @param[in] index - numer wybranego języka GUI
 */
void MainWindow::handleLanguage(int index){
    qApp->removeTranslator(&appTranslator);

    QString languageFile;
    switch(index) {
        case 0:
            languageFile = ":/i18n/data_visualization_app_en_EN.qm";
            break;
        case 1:
            languageFile = ":/i18n/data_visualization_app_pl_PL.qm";
            break;
        case 2:
            languageFile = ":/i18n/data_visualization_app_de_DE.qm";
            break;
    }
 
    if (appTranslator.load(languageFile)) {
        qApp->installTranslator(&appTranslator);
    } else {
        qDebug() << "Nie udało się załadować pliku tłumaczenia: " << languageFile;
    }
}

/**
 * @brief Funkcja do aktualizacji języka interfejsu graficznego
 * 
 * Funkcja reaguje na zdarzenie QEvent::LanguageChange, które jest wysyłane,
 * gdy w aplikacji zostanie zainstalowany nowy obiekt QTranslator. * 
 * @param[in] event - wskaźnik na obiekt zdarzenia
 */
void MainWindow::changeEvent(QEvent *event){
    if (event->type() == QEvent::LanguageChange) {
        ui->retranslateUi(this);
        this->setWindowTitle(tr("ARES Visual Data Panel")); 
        ui->EnterText->setPlaceholderText(tr("enter text..."));
        
        if (isConnected) {
            ui->Connection->setText(tr("Connected"));
        } else{
            ui->Connection->setText(tr("Disconnected"));
        }
    }
    QMainWindow::changeEvent(event);
}

/**
 * @brief Funckja inicjuje procedurę łączenia z wybranym urzadzeniem
 * 
 * Funkcja odpowiada za rozpoczęcie próby połączenia się z urządzenie poprzez bluetooth
 * @param[in] info - dane o urządzeniu bluetooth, z którym następuje połączenie
 */
void MainWindow::connectToDevice(const QBluetoothDeviceInfo &info) {
    qDebug() << "Próba połączenia z:" << info.name();
    bluetoothManager->connectToDevice(info);
}

/**
 * @brief Funckja parsuje odebrane dane surowe i aktualizuje wykresy
 * 
 * Funkcja wyłapuje wartości liczbowe z ciągu znaków przy użyciu wyrażeń regularnych,
 * oczekuje 8 wartości: 2 dla linii, 4 dla czujników ToF oraz 2 dla silników
 * @param[in] data - Tablica bajtów odebrana bezpośrednio z modułu Bluetooth
 */
void MainWindow::onDataReceived(const QByteArray &data) {
    QString recivedData = QString::fromUtf8(data).trimmed();
    qDebug() << "Odebrano z BLE:" << recivedData;

    static const QRegularExpression re("-?\\d+");
    QList<int> values;
    QRegularExpressionMatchIterator i = re.globalMatch(recivedData);

    while (i.hasNext()) {
        QRegularExpressionMatch match = i.next();
        values.append(match.captured(0).toInt());
    }

    if (values.size() == 8) {
        int lines[2] = {values[0], values[1]};
        int tofs[4] = {values[2], values[3], values[4], values[5]};
        int motors[2] = {values[6], values[7]};
        qDebug() << "Sparsowana wiadomość to:" << lines[0] << ", " << lines[1] << " | " << tofs[0] << ", " << tofs[1] << ", " << tofs[2] << ", " << tofs[3] << " | " << motors[0] << ", " << motors[1];// << std::endl;
        line->addMeasurement(lines[0],lines[1]);
        tof->addMeasurement(tofs[0],tofs[1],tofs[2],tofs[3]);
        robot->updateData(motors[0], motors[1], lines[0], lines[1], tofs[0], tofs[1], tofs[2], tofs[3]);
        road->update(motors[0], motors[1], 50.0);
    } else {
        qDebug() << "Wiadomość nie została sparsowana";
        if(bluetoothLogger)
            bluetoothLogger->addReceivedLog(recivedData);
    }
}

/**
 * @brief Funkcja aktualizująca przycisk połączenia
 * 
 * Funkcja zmienia wygląd przycisku połączenia w zależności od statusu połączenia z urządzeniem
 * @param[in] success - informacja o połączeniu (1) /rozłączeniu (0)
 * @param[in] msg - wiadomość otrzymywana od odpowiedniego urządzenia
 */
void MainWindow::onConnectionStatusChanged(bool success, const QString &msg){
    qDebug() << "Status BLE: " << msg;

    if (success && msg == "Gotowy do transmisji") {
        isConnected = true;
        ui->Connection->setText(tr("Connected"));
        ui->Connection->setStyleSheet(
            "background-color: green; color: black; border: 2px solid black;"
            "border-radius: 5px; font-size: 12px; font-weight: bold; padding: 4px 10px;"
        );
    } else if (!success) {
        isConnected = false;
        ui->Connection->setText(tr("Disconnected"));
        ui->Connection->setStyleSheet(
            "background-color: red; color: black; border: 2px solid black;"
            "border-radius: 5px; font-size: 12px; font-weight: bold; padding: 4px 10px;"
        );
    }
}

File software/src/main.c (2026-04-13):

#include <stdio.h>
#include "pico/stdlib.h"
#include "pico/cyw43_arch.h"
#include "btstack.h"
#include "bluetooth_connection.h"
#include "line_detectors.h"
#include "motors.h"
#include "serwo.h"
#include "starter.h"
#include "distance_sensor.h"
#include "controller.h"

static btstack_timer_source_t mess_timer;
static btstack_timer_source_t prog_timer;

static void mess_timer_handler(btstack_timer_source_t *ts) {
    cyw43_arch_gpio_put(CYW43_WL_GPIO_LED_PIN, !cyw43_arch_gpio_get(CYW43_WL_GPIO_LED_PIN));

    // Odczyt czujników 
    int status_left = read_detector_value(Left);
    int status_right = read_detector_value(Right);

    int dystans[4];
    uint8_t addr[4]={0x30, 0x31, 0x32, 0x33};
    for (int i=0; i<4; i++){
        tofSetCurrentAddress(addr[i]);
        dystans[i]=tofReadDistance(i);
        if(dystans[i]>800)
            dystans[i]=800;
    }

    int motor[2];
    for(int i=0; i<2; i++){
        motor[i]=get_motor_value(i);
    }

    // Wysłanie telemetrii przez Bluetooth
    char msg[128]; 
    snprintf(msg, sizeof(msg), "Line %d %d IR %d %d %d %d Motor %d %d\n", status_left, status_right, dystans[0], dystans[1], dystans[2], dystans[3], motor[0], motor[1]);
    printf("%s\n", msg);
    bluetooth_send_telemetry(msg);
 
    // Resetowanie timera
    btstack_run_loop_set_timer(ts, 100);
    btstack_run_loop_add_timer(ts);
}

static void prog_timer_handler(btstack_timer_source_t *ts) {
    exec_program();

    // Resetowanie timera
    btstack_run_loop_set_timer(ts, 1);
    btstack_run_loop_add_timer(ts);
}

#define UART_ID uart1
#define BAUD_RATE 115200

int main()
{
    stdio_init_all();
    sleep_ms(200);
    printf("Ares IS Starting\n");

    if (cyw43_arch_init()) {
        printf("ERROR: cyw43_arch_init failed!\n");
        return 1;
    }

    cyw43_arch_gpio_put(CYW43_WL_GPIO_LED_PIN, 1);
    printf("LED is on\n");

    // Inits
    line_detectors_init();
    motor_init();
    serwo_init();
    IR_init(); 
    starter_init();
    bluetooth_init();

    // Konfiguracja timera dla wiadomości Bluetooth
    mess_timer.process = &mess_timer_handler;
    btstack_run_loop_set_timer(&mess_timer, 500);
    btstack_run_loop_add_timer(&mess_timer);
    printf("Message timer configured\n");

    // Konfiguracja timera dla pracy robota
    prog_timer.process = &prog_timer_handler;
    btstack_run_loop_set_timer(&prog_timer, 1);
    btstack_run_loop_add_timer(&prog_timer);
    printf("Program timer configured\n");

    // Start głównej pętli BTstack
    printf("Starting BTstack main loop\n");
    btstack_run_loop_execute(); 
    return 0;
} 

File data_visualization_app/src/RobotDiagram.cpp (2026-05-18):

/**
 * @file RobotDiagram.cpp
 * @author Jakub Borsukiewicz & Jan Farbotko
 * @brief Klasa do zarządzania widget'em odpowiedzialny za wyświetlanie diagramu robota
 * @version 0.1
 * @date 2026-05-13
 * 
 * @copyright Copyright (c) 2026
 * 
 */
#include "RobotDiagram.hpp"
#include "ui_RobotDiagram.h"
#include <QHBoxLayout>

/**
 * @brief Konstruktor nowego obiektu RobotDiagram
 * 
 *  Konstruktor rysujący cały widget diagramu, na którym są przedstawione wizualnie 
 *  otrzymywane dane z sensorów odległości, czujnika wykrywania linii oraz prędkości silników
 * @param[in] parent - wskaźnik na rodzica obiektu
 */
RobotDiagram::RobotDiagram(QWidget *parent)
    : QWidget(parent)
    , ui(new Ui::RobotDiagram)
{
    ui->setupUi(this);

    this->setStyleSheet("QWidget#RobotDiagram { background-color: #2b2b2b; }");
    
 
    QHBoxLayout *conesLayout = new QHBoxLayout(ui->cones);
    conesLayout->setContentsMargins(0, 0, 0, 0);
    conesLayout->setSpacing(0);



    m_cone1 = new TofConeWidget(this);
    m_cone2 = new TofConeWidget(this);
    m_cone3 = new TofConeWidget(this);
    m_cone4 = new TofConeWidget(this);
 
    m_cone1->setData(800, -20.0);
    m_cone2->setData(800, 0.0);
    m_cone3->setData(800, 0.0);
    m_cone4->setData(800, +20.0);

    std::function<RotatedLabel*(double)> makeTofLabel = [this](double angle) -> RotatedLabel* {
        RotatedLabel *tof = new RotatedLabel(this);
        tof->setText("800 mm");
        tof->setAngle(angle);
        return tof;
    };

    m_labelTof1 = makeTofLabel(-20.0);
    m_labelTof2 = makeTofLabel(0.0);
    m_labelTof3 = makeTofLabel(0.0);
    m_labelTof4 = makeTofLabel(+20.0);

    std::function<QVBoxLayout*(TofConeWidget*, RotatedLabel*)> makePair = [this](TofConeWidget *cone, RotatedLabel *lbl) -> QVBoxLayout* {
    QVBoxLayout *v = new QVBoxLayout();
    v->setContentsMargins(0, 0, 0, 0);
    v->setSpacing(0);

    v->addWidget(cone, 1);

    QWidget *lblContainer = new QWidget(this);
    lblContainer->setStyleSheet("background-color: #2255AA;");
    QHBoxLayout *lh = new QHBoxLayout(lblContainer);
    lh->setContentsMargins(0, 0, 0, 0);
    lh->addWidget(lbl, 0, Qt::AlignHCenter);

    v->addWidget(lblContainer, 0);
    return v;
};


    conesLayout->addLayout(makePair(m_cone1, m_labelTof1));
    conesLayout->addLayout(makePair(m_cone2, m_labelTof2));
    conesLayout->addLayout(makePair(m_cone3, m_labelTof3));
    conesLayout->addLayout(makePair(m_cone4, m_labelTof4));

    ui->distance_sensors->setVisible(false);
    ui->distance_sensors->setFixedHeight(0);

    ui->mainBody->setStyleSheet("QWidget#mainBody { background-color: #87CEEB; }");
    ui->Motors->setContentsMargins(4, 4, 4, 12);
    ui->verticalLayout->setContentsMargins(30, 0, 30, 20);
    ui->verticalLayout->setSpacing(0);


        const QString lineStyle =
        "QLabel {"
        "  background-color: #55CC00;"
        "  border: 2px solid #336600;"
        "  border-radius: 6px;"
        "  font-size: 13px;"
        "  font-weight: bold;"
        "  color: #1a3300;"
        "}";
 
    ui->LineL->setFixedSize(80, 44);
    ui->LineL->setAlignment(Qt::AlignCenter);
    ui->LineL->setStyleSheet(lineStyle);
    ui->LineL->setText("0");
 
    ui->LineR->setFixedSize(80, 44);
    ui->LineR->setAlignment(Qt::AlignCenter);
    ui->LineR->setStyleSheet(lineStyle);
    ui->LineR->setText("0");

        const QString motorStyle =
        "QLabel {"
        "  background-color: #1a2a4a;"
        "  border: 2px solid #0a0a0a;"
        "  border-radius: 10px;"
        "  font-size: 14px;"
        "  font-weight: bold;"
        "  color: white;"
        "}";
 
    ui->MotorL->setFixedSize(80, 60);
    ui->MotorL->setAlignment(Qt::AlignCenter);
    ui->MotorL->setStyleSheet(motorStyle);
    ui->MotorL->setText("0 %");
 
    ui->MotorR->setFixedSize(80, 60);
    ui->MotorR->setAlignment(Qt::AlignCenter);
    ui->MotorR->setStyleSheet(motorStyle);
    ui->MotorR->setText("0 %");
 
    ui->Motors->setContentsMargins(4, 0, 4, 4);
    ui->Motors->setSpacing(6);

    m_arrowL = ui->ArrowL;
    m_arrowR = ui->ArrowR;
    m_arrowL->setFixedSize(50, 60);
    m_arrowR->setFixedSize(50, 60);


}

/**
 * @brief Destruktor obiektu RobotDiagram
 * 
 */
RobotDiagram::~RobotDiagram()
{
    delete ui;
}

/**
 * @brief Funkcja aktualizująca wyświetlane dane z czujników
 * 
 * Funkcja aktualizuje wizualne elemnty widgetu na podstawie zmieniających się danych z czujników
 * 
 * @param[in] MotorL - prędkość lewego silnika
 * @param[in] MotorR - prędkość prawego silnika
 * @param[in] LineL - warość lewego czujnika linii
 * @param[in] LineR - wartość prawego czujnika linii
 * @param[in] tof1 - wartość czujnika odległości nr 1 (lewy skrajny)
 * @param[in] tof2 - wartość czujnika odległości nr 2 (lewy środkowy)
 * @param[in] tof3 - wartość czujnika odległości nr 3 (prawy środkowy)
 * @param[in] tof4 - wartość czujnika odległości nr 4 (prawy skrajny)
 */
void RobotDiagram::updateData(int MotorL, int MotorR, int LineL, int LineR, int tof1, int tof2, int tof3, int tof4){
    m_cone1->setData(tof1, -20.0);
    m_cone2->setData(tof2, 0.0);
    m_cone3->setData(tof3, 0.0);
    m_cone4->setData(tof4, 20.0);

    m_labelTof1->setText(QString("%1 mm").arg(tof1));
    m_labelTof2->setText(QString("%1 mm").arg(tof2));
    m_labelTof3->setText(QString("%1 mm").arg(tof3));
    m_labelTof4->setText(QString("%1 mm").arg(tof4));

    m_arrowL->setSpeed(MotorL);
    m_arrowR->setSpeed(MotorR);

    lastMotorL = MotorL;
    lastMotorR = MotorR;
    lastLineL = LineL;
    lastLineR = LineR;

    updateLabelsText();
}

/**
 * @brief Funkcja pomocnicza do aktualizacji danych na czujnikach
 * 
 */
void RobotDiagram::updateLabelsText() {
    ui->MotorL->setText(tr("Motor left:") + "\n" + QString::number(qAbs(lastMotorL)) + " %");
    ui->MotorR->setText(tr("Motor right:") + "\n" + QString::number(qAbs(lastMotorR)) + " %");
    
    ui->LineL->setText(tr("Left line:") + "\n" + QString::number(lastLineL));
    ui->LineR->setText(tr("Right line:") + "\n" + QString::number(lastLineR));
}

/**
 * @brief Funkcja do aktualizacji języka interfejsu graficznego
 * 
 * Funkcja reaguje na zdarzenie QEvent::LanguageChange, które jest wysyłane,
 * gdy w aplikacji zostanie zainstalowany nowy obiekt QTranslator. * 
 * @param[in] event - wskaźnik na obiekt zdarzenia
 */
void RobotDiagram::changeEvent(QEvent *event){
    if(event->type() == QEvent::LanguageChange) {
        ui->retranslateUi(this); 

        updateLabelsText();
    }
    QWidget::changeEvent(event); 
}

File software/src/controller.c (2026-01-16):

#include "pico/stdlib.h"
#include <stdio.h> 
#include "controller.h"
#include "line_detectors.h"
#include "motors.h"
#include "serwo.h"
#include "distance_sensor.h"
#include "starter.h"
#include "bluetooth_connection.h"

bool beginning = true;
bool ending = false;
side_t lastSeen = left;

void anti_out_system(line_detector_t status){
    if(status == Both){
        motor_set(Left_Motor, Backward, 100);
        motor_set(Right_Motor, Backward, 100);
        sleep_ms(1500);
        if(lastSeen == left){
            motor_set(Left_Motor, Backward, 80);       
            motor_set(Right_Motor, Forward, 80); 
        }else{
            motor_set(Left_Motor, Forward, 80);       
            motor_set(Right_Motor, Backward, 80); 
        }
    }else if(status == Left){
        motor_set(Left_Motor, Backward, 100);
        motor_set(Right_Motor, Backward, 70);
        sleep_ms(1000);
        motor_set(Left_Motor, Forward, 80);
        motor_set(Right_Motor, Backward, 80);
    }else{
        motor_set(Left_Motor, Backward, 70);
        motor_set(Right_Motor, Backward, 100);
        sleep_ms(1000);
        motor_set(Left_Motor, Backward, 80);
        motor_set(Right_Motor, Forward, 80);
    }
}

void fighting_stage(){
    int irData[4];
    uint8_t addr[4]={0x30, 0x31, 0x32, 0x33};           // 0 - lewy, 1 - lewy przód, 2 - prawy przód, 3 - prawy
    for (int i=0; i<4; i++){
        tofSetCurrentAddress(addr[i]);
        irData[i]=tofReadDistance(i);
    }

    if(irData[0]>TOF_OUT_OF_RANGE && irData[1]>TOF_OUT_OF_RANGE && irData[2]>TOF_OUT_OF_RANGE && irData[3]>TOF_OUT_OF_RANGE){       // nie widać przeciwnika
        
        if(lastSeen == left){
            motor_set(Left_Motor, Backward, 80);       
            motor_set(Right_Motor, Forward, 80); 
        }else{
            motor_set(Left_Motor, Forward, 80);       
            motor_set(Right_Motor, Backward, 80); 
        }
    }else if(irData[1]<ENEMY_CLOSE && irData[2]<ENEMY_CLOSE){               // przeciwnik bardzo blisko        
        motor_set(Left_Motor, Forward, 100);       
        motor_set(Right_Motor, Forward, 100);     
    }else if(irData[3]-irData[0]>SIDE_TRESHOLD){                            // przeciwnik bardziej na lewo
        motor_set(Left_Motor, Forward, 40);       
        motor_set(Right_Motor, Forward, 100); 
        lastSeen = left;
    }else if(irData[0]-irData[3]>SIDE_TRESHOLD){                            // przeciwnik bardziej na prawo
        motor_set(Left_Motor, Forward, 100);       
        motor_set(Right_Motor, Forward, 40); 
        lastSeen = right;
    }else{                                                                  // prosto
        motor_set(Left_Motor, Forward, 80);       
        motor_set(Right_Motor, Forward, 80); 
    }
}


void exec_program(){
    State state = getState();
    
    if(state == Fighting){
        if(beginning){
            char msg[64];
            snprintf(msg, sizeof(msg), "Zaczynam walke\n");
            bluetooth_send_telemetry(msg);

            beginning = false;
            ending = false;
            sleep_ms(3000);
            motor_set(Left_Motor, Backward, 80); 
            motor_set(Right_Motor, Forward, 80);       
            sleep_ms(800);                             
            serwo_set_posiotion(LEFT_SERWO, 170);
            serwo_set_posiotion(RIGHT_SERWO, 10);
        }

        line_detector_t lineDetectorStatus = check_line_detectors();
        if(lineDetectorStatus != None){
            int status_right = read_detector_value(Right);
            char msg[64];
            snprintf(msg, sizeof(msg), "Wykryto linie, %d\n", status_right);
            bluetooth_send_telemetry(msg);

            anti_out_system(lineDetectorStatus);
        }

        fighting_stage();

    }else if(state == End){
        if(!ending){
            char msg[64];
            snprintf(msg, sizeof(msg), "Koniec walki\n");
            bluetooth_send_telemetry(msg);

            ending = true;
            beginning = true;
            all_motor_stop();
            serwo_set_posiotion(LEFT_SERWO, 90);
            serwo_set_posiotion(RIGHT_SERWO, 90);
        }
    }
}

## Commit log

2025-10-31 zamodelowano koła robota
    [forma_do_kół.ipt, koło.0001.ipt, koło.ipt]
2025-10-31 Update kół oraz obudowa robota ver1.0
    [koło.0001.ipt, koło.0004.ipt, koło.ipt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]
2025-10-31 Minisumo mechanika ver1.1
    [góra_robota.ipt, koło.0004.ipt, minisumo_złożenie.0002.iam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]
2025-11-04 Mechanica ver1.3 oraz pliki stl do druku 3D
    [forma_do_kół.stl, góra_robota.ipt, góra_robota.stl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]
2025-11-12 Dodano koła do złożenia robota oraz update plików .gitignore
    [minisumo_złożenie.iam, opona.ipt]
2025-11-13 first schematics
    [ARES.PrjPcb, Main_board.SchDoc, Raspberry_main.SchDoc]
2025-11-13 more schematics
    [IR_Sensor_Block.SchDoc, Line_Sensor.SchDoc, Motor_driver.SchDoc]
2025-11-14 last schematics
    [Serwo.SchDoc, Starter.SchDoc]
2025-11-14 Finished PCB
    [PCB.PcbDoc]
2025-11-16 IR sensors part 1
2025-12-02 added motors code
2025-12-13 Added Serwo and fixed Motors
    [main.c, motors.c, motors.h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]
2026-01-13 dodanie modelu robota w ROS2
    [robot.urdf.xacro]
2026-01-14 update modelu robota
    [robot.urdf.xacro]
2026-01-14 zaktualizowano cały model robota
    [body.STL, robot.urdf.xacro, wheel.STL]
2026-05-11 add robotdiagram - motors and lines
